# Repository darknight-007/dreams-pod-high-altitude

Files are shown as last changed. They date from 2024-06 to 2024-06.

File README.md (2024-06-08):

# High-Altitude Balloon Payload with Attitude Control and Predictive Scheduling for Aerobiological Sampling and Environmental Monitoring

**Jnaneshwar Das, School of Earth and Space Exploration**

**Other contributors:**  
*EarthPod sensor probe* – Cole Bauer, Katrina Davis, Darwin Mick, Desmond Hanaan, Elizabeth Trembath-Reichert  
*Balloon payload considerations* – Scott Clemens, Anyell Mata, Tom Sharp

## Introduction

We introduce a lightweight, low SWaP (< 1.5 kg) high-altitude balloon payload for aerobiological sampling. The innovation incorporates the latest drone flight control technologies and custom environmental sensing hardware. A ground-tested prototype for the payload has been designed.

## Description

The main body, inspired by the CubeSat design format and quadrotor drone layout, consists of multiple levels interconnected with load-bearing aluminum spacers. 

- **Level 6**: Houses a Pixhawk flight controller running the PX4 flight stack, and a GPS and compass module.
- **Level 5**: Accommodates an aerobiological sampling payload capable of collecting air samples and storing them in filtrates, triggered by onboard compute for adaptive sampling.
- **Level 4**: Features the EarthPod sensor probe, which conducts various atmospheric measurements, including relative humidity, temperature, wind speed and direction, and light intensity/flux, and is capable of decision-making using an onboard Arduino Feather.
- **Level 3**: Contains two reaction wheels for stabilizing yaw angle (heading) to point in a desired direction, such as imaging specific ground features with a pitch-gimbaled multi-spectral camera and spectrometer imaging payload with onboard compute.
- **Level 2**: Houses two 4S lithium-polymer batteries to power the system's various components.
- **Level 1 (Bottom)**: Contains the imaging system and yaw stabilization of the tower and pitch stabilization of the gimbal mechanism managed by the Pixhawk flight controller on level 6. Also houses a radio telemetry link and antenna, connected to the flight controller on level 6. The payload is suspended using a load-bearing 360-degree swivel.







In some manifestations, solar panels can be added to one or more sides of the payload tower, and the yaw stabilization system can ensure the panels are on average directed at the sun. Yaw stabilization can also enable imaging of the sun with a top-mounted camera, or tracking features such as solar eclipse shadows. The payload can also be used as a ground-based sensor probe, in a sensor network format, especially where long-term autonomy and attitude stabilization are desired. All decision-making happens onboard the payload, with computations split between flight controller (guidance, navigation, and control), EarthPod sensor probe (atmospheric and aerobiological sampling), and Intel Atom or ARM compute to carry out image processing tasks. A bank of lithium polymer batteries power the system and can be recharged with actively oriented solar panels that can be reoriented by the yaw stabilization system.



## Demo Video

Demo video, sun-tracking during partial solar eclipse in Phoenix:  
(https://github.com/darknight-007/dreams-pod-high-altitude/assets/3958994/a45d4cd9-dda4-4b37-beda-d7d8ff1691a0){:target="_blank"}

Video of sun-tracking experiment at ground level during April 8 partial solar eclipse in Arizona:  
[Watch on YouTube](https://www.youtube.com/shorts/dlAszII4H6c){:target="_blank"}

## Tested Environment

Tested using ROS2 Humble, on Ubuntu 22.04 running on Hardkernel Odroid M1, required ROS packages, mavros, mavros-extras.

## Funding Acknowledgements

NASA Flight Opportunities Tech Flights (Lunar Lander ExoCam), NSF CNS 152161, Behar endowment funds, Earth Innovation Hub Corp. (501c3).

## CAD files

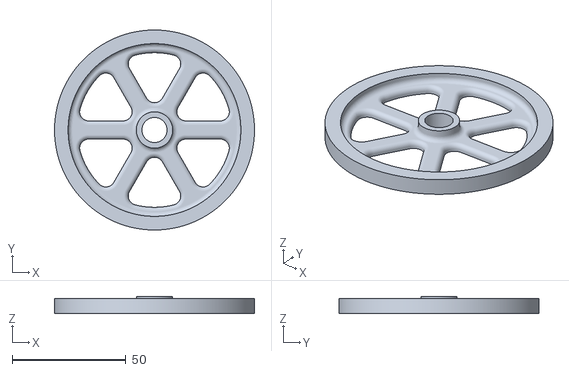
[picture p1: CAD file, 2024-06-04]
three and half fly wheel std 0.01.stl
88.0 x 88.0 x 7.50

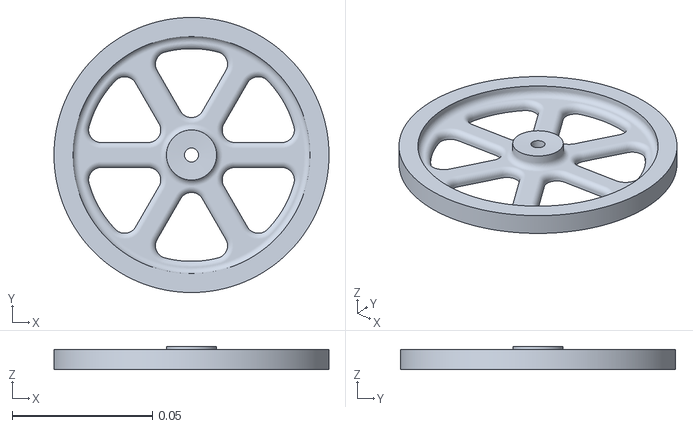
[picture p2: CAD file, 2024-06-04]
wheel-v2-feb-2024.stl
0.0981 x 0.0981 x 0.00836

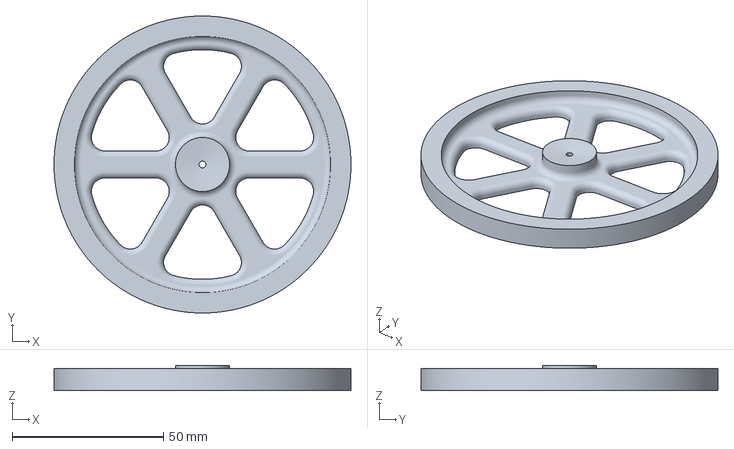
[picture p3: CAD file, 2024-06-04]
wheel-for-print.3mf
98.1 x 98.1 x 8.36 mm

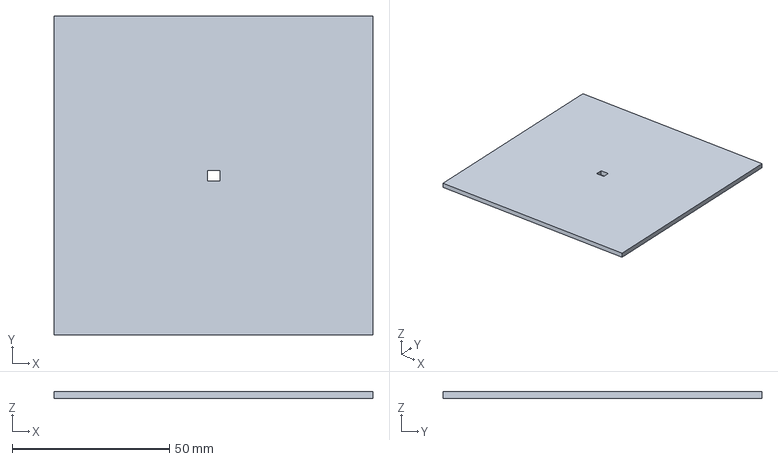
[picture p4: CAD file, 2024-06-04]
plates-wheel.3mf
101.3 x 101.3 x 2.12 mm

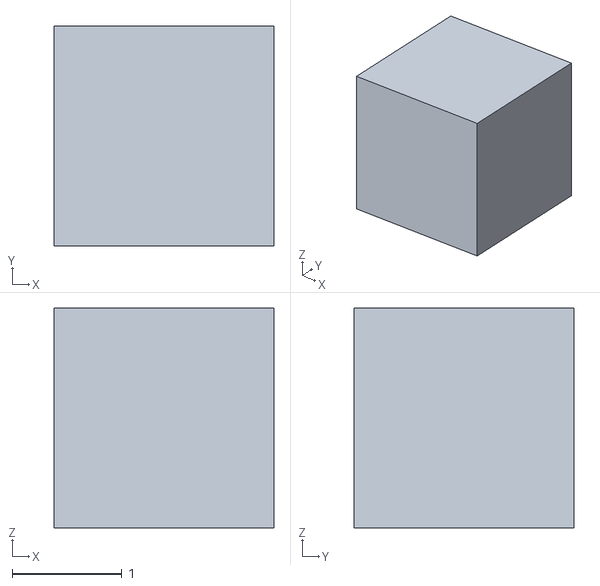
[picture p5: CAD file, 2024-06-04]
wheel.stl
2.00 x 2.00 x 2.00

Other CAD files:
wheel-v2-feb-2024-center-hole-widened-4.stl
plate-wheel.blend
plates-wheel.stl
wheel-for-print.stl

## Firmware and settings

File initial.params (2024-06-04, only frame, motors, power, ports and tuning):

1	1	BAT1_A_PER_V	17.000000000000000000	9
1	1	BAT1_CAPACITY	-1.000000000000000000	9
1	1	BAT1_I_CHANNEL	-1	6
1	1	BAT1_N_CELLS	0	6
1	1	BAT1_R_INTERNAL	0.004999999888241291	9
1	1	BAT1_SOURCE	0	6
1	1	BAT1_V_CHANNEL	-1	6
1	1	BAT1_V_CHARGED	4.050000190734863281	9
1	1	BAT1_V_DIV	10.100000381469726563	9
1	1	BAT1_V_EMPTY	3.599999904632568359	9
1	1	BAT1_V_LOAD_DROP	0.100000001490116119	9
1	1	BAT_AVRG_CURRENT	15.000000000000000000	9
1	1	BAT_CRIT_THR	0.070000000298023224	9
1	1	BAT_EMERGEN_THR	0.050000000745058060	9
1	1	BAT_LOW_THR	0.150000005960464478	9
1	1	BAT_N_CELLS	3	6
1	1	BAT_V_CHARGED	4.050000190734863281	9
1	1	BAT_V_EMPTY	3.599999904632568359	9
1	1	BAT_V_LOAD_DROP	0.300000011920928955	9
1	1	BAT_V_OFFS_CURR	0.000000000000000000	9
1	1	CA_AIRFRAME	0	6
1	1	CA_ROTOR0_AX	0.000000000000000000	9
1	1	CA_ROTOR0_AY	0.000000000000000000	9
1	1	CA_ROTOR0_AZ	-1.000000000000000000	9
1	1	CA_ROTOR0_CT	6.500000000000000000	9
1	1	CA_ROTOR0_KM	0.050000000745058060	9
1	1	CA_ROTOR0_PX	0.150000005960464478	9
1	1	CA_ROTOR0_PY	0.150000005960464478	9
1	1	CA_ROTOR0_PZ	0.000000000000000000	9
1	1	CA_ROTOR10_AX	0.000000000000000000	9
1	1	CA_ROTOR10_AY	0.000000000000000000	9
1	1	CA_ROTOR10_AZ	-1.000000000000000000	9
1	1	CA_ROTOR10_CT	6.500000000000000000	9
1	1	CA_ROTOR10_KM	0.050000000745058060	9
1	1	CA_ROTOR10_PX	0.000000000000000000	9
1	1	CA_ROTOR10_PY	0.000000000000000000	9
1	1	CA_ROTOR10_PZ	0.000000000000000000	9
1	1	CA_ROTOR11_AX	0.000000000000000000	9
1	1	CA_ROTOR11_AY	0.000000000000000000	9
1	1	CA_ROTOR11_AZ	-1.000000000000000000	9
1	1	CA_ROTOR11_CT	6.500000000000000000	9
1	1	CA_ROTOR11_KM	0.050000000745058060	9
1	1	CA_ROTOR11_PX	0.000000000000000000	9
1	1	CA_ROTOR11_PY	0.000000000000000000	9
1	1	CA_ROTOR11_PZ	0.000000000000000000	9
1	1	CA_ROTOR1_AX	0.000000000000000000	9
1	1	CA_ROTOR1_AY	0.000000000000000000	9
1	1	CA_ROTOR1_AZ	-1.000000000000000000	9
1	1	CA_ROTOR1_CT	6.500000000000000000	9
1	1	CA_ROTOR1_KM	0.050000000745058060	9
1	1	CA_ROTOR1_PX	-0.150000005960464478	9
1	1	CA_ROTOR1_PY	-0.150000005960464478	9
1	1	CA_ROTOR1_PZ	0.000000000000000000	9
1	1	CA_ROTOR2_AX	0.000000000000000000	9
1	1	CA_ROTOR2_AY	0.000000000000000000	9
1	1	CA_ROTOR2_AZ	-1.000000000000000000	9
1	1	CA_ROTOR2_CT	6.500000000000000000	9
1	1	CA_ROTOR2_KM	-0.050000000745058060	9
1	1	CA_ROTOR2_PX	0.150000005960464478	9
1	1	CA_ROTOR2_PY	-0.150000005960464478	9
1	1	CA_ROTOR2_PZ	0.000000000000000000	9
1	1	CA_ROTOR3_AX	0.000000000000000000	9
1	1	CA_ROTOR3_AY	0.000000000000000000	9
1	1	CA_ROTOR3_AZ	-1.000000000000000000	9
1	1	CA_ROTOR3_CT	6.500000000000000000	9
1	1	CA_ROTOR3_KM	-0.050000000745058060	9
1	1	CA_ROTOR3_PX	-0.150000005960464478	9
1	1	CA_ROTOR3_PY	0.150000005960464478	9
1	1	CA_ROTOR3_PZ	0.000000000000000000	9
1	1	CA_ROTOR4_AX	0.000000000000000000	9
1	1	CA_ROTOR4_AY	0.000000000000000000	9
1	1	CA_ROTOR4_AZ	-1.000000000000000000	9
1	1	CA_ROTOR4_CT	6.500000000000000000	9
1	1	CA_ROTOR4_KM	0.050000000745058060	9
1	1	CA_ROTOR4_PX	0.000000000000000000	9
1	1	CA_ROTOR4_PY	0.000000000000000000	9
1	1	CA_ROTOR4_PZ	0.000000000000000000	9
1	1	CA_ROTOR5_AX	0.000000000000000000	9
1	1	CA_ROTOR5_AY	0.000000000000000000	9
1	1	CA_ROTOR5_AZ	-1.000000000000000000	9
1	1	CA_ROTOR5_CT	6.500000000000000000	9
1	1	CA_ROTOR5_KM	0.050000000745058060	9
1	1	CA_ROTOR5_PX	0.000000000000000000	9
1	1	CA_ROTOR5_PY	0.000000000000000000	9
1	1	CA_ROTOR5_PZ	0.000000000000000000	9
1	1	CA_ROTOR6_AX	0.000000000000000000	9
1	1	CA_ROTOR6_AY	0.000000000000000000	9
1	1	CA_ROTOR6_AZ	-1.000000000000000000	9
1	1	CA_ROTOR6_CT	6.500000000000000000	9
1	1	CA_ROTOR6_KM	0.050000000745058060	9
1	1	CA_ROTOR6_PX	0.000000000000000000	9
1	1	CA_ROTOR6_PY	0.000000000000000000	9
1	1	CA_ROTOR6_PZ	0.000000000000000000	9
1	1	CA_ROTOR7_AX	0.000000000000000000	9
1	1	CA_ROTOR7_AY	0.000000000000000000	9
1	1	CA_ROTOR7_AZ	-1.000000000000000000	9
1	1	CA_ROTOR7_CT	6.500000000000000000	9
1	1	CA_ROTOR7_KM	0.050000000745058060	9
1	1	CA_ROTOR7_PX	0.000000000000000000	9
1	1	CA_ROTOR7_PY	0.000000000000000000	9
1	1	CA_ROTOR7_PZ	0.000000000000000000	9
1	1	CA_ROTOR8_AX	0.000000000000000000	9
1	1	CA_ROTOR8_AY	0.000000000000000000	9
1	1	CA_ROTOR8_AZ	-1.000000000000000000	9
1	1	CA_ROTOR8_CT	6.500000000000000000	9
1	1	CA_ROTOR8_KM	0.050000000745058060	9
1	1	CA_ROTOR8_PX	0.000000000000000000	9
1	1	CA_ROTOR8_PY	0.000000000000000000	9
1	1	CA_ROTOR8_PZ	0.000000000000000000	9
1	1	CA_ROTOR9_AX	0.000000000000000000	9
1	1	CA_ROTOR9_AY	0.000000000000000000	9
1	1	CA_ROTOR9_AZ	-1.000000000000000000	9
1	1	CA_ROTOR9_CT	6.500000000000000000	9
1	1	CA_ROTOR9_KM	0.050000000745058060	9
1	1	CA_ROTOR9_PX	0.000000000000000000	9
1	1	CA_ROTOR9_PY	0.000000000000000000	9
1	1	CA_ROTOR9_PZ	0.000000000000000000	9
1	1	CA_ROTOR_COUNT	4	6
1	1	MC_PITCHRATE_D	0.003000000026077032	9
1	1	MC_PITCHRATE_FF	0.000000000000000000	9
1	1	MC_PITCHRATE_I	0.200000002980232239	9
1	1	MC_PITCHRATE_K	1.000000000000000000	9
1	1	MC_PITCHRATE_MAX	220.000000000000000000	9
1	1	MC_PITCHRATE_P	0.150000005960464478	9
1	1	MC_PITCH_P	6.500000000000000000	9
1	1	MC_ROLLRATE_D	0.003000000026077032	9
1	1	MC_ROLLRATE_FF	0.000000000000000000	9
1	1	MC_ROLLRATE_I	0.200000002980232239	9
1	1	MC_ROLLRATE_K	1.000000000000000000	9
1	1	MC_ROLLRATE_MAX	220.000000000000000000	9
1	1	MC_ROLLRATE_P	0.150000005960464478	9
1	1	MC_ROLL_P	6.500000000000000000	9
1	1	MC_YAWRATE_D	0.000000000000000000	9
1	1	MC_YAWRATE_FF	0.000000000000000000	9
1	1	MC_YAWRATE_I	0.100000001490116119	9
1	1	MC_YAWRATE_K	1.000000000000000000	9
1	1	MC_YAWRATE_MAX	200.000000000000000000	9
1	1	MC_YAWRATE_P	0.200000002980232239	9
1	1	MC_YAW_P	2.799999952316284180	9
1	1	MC_YAW_WEIGHT	0.400000005960464478	9
1	1	MOT_POLE_COUNT	14	6
1	1	MOT_SLEW_MAX	0.000000000000000000	9
1	1	PWM_MAIN_DIS1	1000	6
1	1	PWM_MAIN_DIS2	1000	6
1	1	PWM_MAIN_DIS3	1000	6
1	1	PWM_MAIN_DIS4	1000	6
1	1	PWM_MAIN_DIS5	1000	6
1	1	PWM_MAIN_DIS6	1000	6
1	1	PWM_MAIN_DIS7	1000	6
1	1	PWM_MAIN_DIS8	1000	6
1	1	PWM_MAIN_FAIL1	-1	6
1	1	PWM_MAIN_FAIL2	-1	6
1	1	PWM_MAIN_FAIL3	-1	6
1	1	PWM_MAIN_FAIL4	-1	6
1	1	PWM_MAIN_FAIL5	-1	6
1	1	PWM_MAIN_FAIL6	-1	6
1	1	PWM_MAIN_FAIL7	-1	6
1	1	PWM_MAIN_FAIL8	-1	6
1	1	PWM_MAIN_FUNC1	101	6
1	1	PWM_MAIN_FUNC2	103	6
1	1	PWM_MAIN_FUNC3	102	6
1	1	PWM_MAIN_FUNC4	104	6
1	1	PWM_MAIN_FUNC5	0	6
1	1	PWM_MAIN_FUNC6	0	6
1	1	PWM_MAIN_FUNC7	0	6
1	1	PWM_MAIN_FUNC8	421	6
1	1	PWM_MAIN_MAX1	1900	6
1	1	PWM_MAIN_MAX2	1900	6
1	1	PWM_MAIN_MAX3	1900	6
1	1	PWM_MAIN_MAX4	1900	6
1	1	PWM_MAIN_MAX5	2000	6
1	1	PWM_MAIN_MAX6	2000	6
1	1	PWM_MAIN_MAX7	2000	6
1	1	PWM_MAIN_MAX8	2000	6
1	1	PWM_MAIN_MIN1	1100	6
1	1	PWM_MAIN_MIN2	1100	6
1	1	PWM_MAIN_MIN3	1100	6
1	1	PWM_MAIN_MIN4	1100	6
1	1	PWM_MAIN_MIN5	1000	6
1	1	PWM_MAIN_MIN6	1000	6
1	1	PWM_MAIN_MIN7	1000	6
1	1	PWM_MAIN_MIN8	1000	6
1	1	PWM_MAIN_TIM0	400	6
1	1	PWM_MAIN_TIM1	400	6
1	1	PWM_MAIN_TIM2	400	6
1	1	SYS_AUTOSTART	4001	6

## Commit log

2024-03-18 Create test-pitch-servo-control.py
    ros2 node to map payload pitch to PX4 mount pitch control using gimbal propotocl, through mavros.
2024-03-19 Create test-offboard-control-pitch-yaw-tracking.py
    initial commit for solar eclipse testing
2024-03-19 Update test-offboard-control-pitch-yaw-tracking.py
    moving thrust control (momentum wheels collective speed) to a PID control paradigm, operating on yaw error and error rates.
2024-03-20 Update test-offboard-control-pitch-yaw-tracking.py
    tinkering with PD control on thrust
2024-03-20 Create test-offboard-yaw-pitch-tracking-rate-control.py
    initial commit, uses body_rate yaw to control heading
2024-03-20 Create test-offboard-velocity-yaw-pitch-control-timer.py
    initial commit, a timer updates yaw by chosen increments, for tracking test
2024-03-25 Update test-uxrce-dds-attitude-control.py
    added gimbal mount control code
2024-03-31 Update test-uxrce-dds-attitude-control.py
    fixed setpoint FRD frames
    compass rotation, pitch 90
2024-04-08 Create test-mavros-offboard-rate-control-yaw-pitch-spot-tracking.py
    subscribes to brigtest spot opencv node, and uses normalized x coord of brightest spot as yaw rate setpoint.
2024-04-09 Update test-offboard-control-pitch-yaw-tracking.py
    Tested on solar eclipse day, stabilizes payload/camera yaw/pitch.
2024-04-10 Create test-polar-vector-publisher.py
    initial commit for yaw pitch vector publisher, for scene scan
2024-04-10 Create test-helical-polar-vector-publisher.py
    initial commit - yaw pitch scanner, using stepping helical pattern
2024-06-04 Add files via upload
    making things upto date
    [attitude_brightness_data.csv, initial.params]
2024-06-04 Add files via upload
    CAD files for wheels
    [plate-wheel.blend, plates-wheel.3mf, plates-wheel.stl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]
2024-06-05 Delete wheel-for-print_0.1mm_PETG_MK3S_5h15m.gcode
    redundant
2024-06-05 Delete wheel.blend1
    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
2024-06-05 Delete wheel-v2-feb-2024.blend1
    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
2024-06-05 Delete wheel-v2-feb-2024-v2.blend1
    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
2024-06-05 Delete wheel-v2-feb-2024-center-hole-widened-3.stl
    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
    [wheel-v2-feb-2024-center-hole-widened-3.stl]
2024-06-05 Delete wheel-v2-feb-2024-center-hole-widened-2.stl
    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
    [wheel-v2-feb-2024-center-hole-widened-2.stl]
2024-06-05 Delete wheel-v2-feb-2024-center-hole-widened-1.stl
    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
    [wheel-v2-feb-2024-center-hole-widened-1.stl]
